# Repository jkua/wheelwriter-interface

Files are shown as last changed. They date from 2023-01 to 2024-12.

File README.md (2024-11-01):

# Low-level IBM Wheelwriter interface
This project is to build a low-level interface for an IBM Wheelwriter 
typewriter. This builds on work by 
[tofergregg](https://github.com/tofergregg/IBM-Wheelwriter-Hack), 
[RussellSenior](https://github.com/tofergregg/IBM-Wheelwriter-Hack/pull/11), 
and [jim11662418](https://github.com/jim11662418/wheelwriter-teletype) 
who figured out the internal serial communication bus and the protocol it uses.

This project was built and tested on an IBM Wheelwriter 3. Likely this will 
work on at least Series I Wheelwriters (3/5/6), and possibly later models as 
well.

## Architecture
This project consists of:

1. [Hardware interface module](pcb/) - this attaches to the back of the Wheelwriter as
the OEM printer option did, and connect to the 10-pin option connector located 
behind the 70 mm-wide hinged panel on the top rear of the typewriter. The core 
electronics are an [Arduino Nano RP2040 Connect](https://docs.arduino.cc/hardware/nano-rp2040-connect)
mounted on a custom PCB to interface with the Wheelwriter's option connector. 

3. [Arduino Wheelwriter driver](src/arduino/wheelwriter_interface) - this 
communicates with the Wheelwriter over the serial bus and provide low-level 
control of the typewriter, including platen and carriage positioning and 
typehead imprinting.

4. [REST API](docs/wwib_rest_api.md) service - the built-in WiFi connectivity 
on the Nano supports a web server which allows a modern computer, smartphone, 
or tablet to control the typewriter via the interface module.

5. [Python serial client](src/client) - PC client to talk to the Arduino and
allow it to send text to print as well as relay raw Wheelwriter commands. 

6. REST Client software - this software will demonstrate the use of the REST API

## Related work
[IBM-Wheelwriter-Hack](https://github.com/tofergregg/IBM-Wheelwriter-Hack) by 
Chris Gregg/[tofergregg](https://github.com/tofergregg) is what initially 
inspired me to look into Wheelwriters. His [videos](https://www.youtube.com/watch?v=Awxbu8y5cv8) 
[on](https://www.youtube.com/watch?v=0vrvDQmZcPI) 
[YouTube](https://www.youtube.com/watch?v=5FTS4fj5Im4) showed his work on 
reverse engineering the Wheelwriter's bus with a logic analyzer in about 2017.
His implementation bit-bangs a TX line to drive a N-channel MOSFET.

Be sure to check out his 
[Smith Corona typewriter to printer conversion](https://www.youtube.com/watch?v=le4C2HeNrdQ)!

Ryan Jarvis/[Cabalist](https://github.com/Cabalist) provided a 
[complete printwheel mapping](https://github.com/tofergregg/IBM-Wheelwriter-Hack/issues/5) 
for US language printwheels.

[Russell Senior](https://github.com/RussellSenior) made the connection that 
this is an Intel 8051 9-bit serial bus in mode 2 and provided a 
[great wiki page](https://github.com/RussellSenior/IBM-Wheelwriter-Hack/wiki/Bus-Protocol) 
describing a great deal of the command set.

[jim11662418](https://github.com/jim11662418) created implementations for 
the 8051 compatible [Dallas Semi DS89C440](https://github.com/jim11662418/wheelwriter-printer)
and [STC Micro STC15W4K32S4](https://github.com/jim11662418/wheelwriter-teletype)
that are very nice.

[MicroCoreLabs](https://github.com/MicroCoreLabs) created an 
[Lattice FPGA implementation](https://github.com/MicroCoreLabs/Projects/tree/master/Wheelwriter) 
and an [Arduino Leonardo implementation](https://github.com/MicroCoreLabs/Projects/tree/master/Wheelwriter2). 
Both implement a serial port that translates an ASCII character stream to motor 
controller commands. The Arduino implementation directly uses the ATmega32u4's 
UART an interestingly toggles the transmitter off when not sending. 
[Here's a YouTube video](https://www.youtube.com/watch?v=q8gCYw75E1A) of the 
FPGA version running.

[CadetWriter](https://github.com/IBM-1620/Cadetwriter) is an effort by Dave 
Babcock and Stephen Casner to interface to a Wheelwriter 1000 by instead 
sitting between the keyboard and the logic controller. This work was developed 
to build a general-purpose ASCII terminal.

[Generative Daily Planner](https://www.thingswemake.com/generative-daily-planner)
([Github](https://github.com/joshsucher/wheelwriter-gpt-agenda)) by Josh 
Sucher, is a "GPT-4-powered bot that ingests email, calendar and contacts from 
a range of sources (mainly Gmail, Gcal and iCloud) and outputs a daily agenda" 
and utilizes code from this repo.

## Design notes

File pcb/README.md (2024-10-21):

# Wheelwriter Interface Board

There are two versions of the Wheelwriter Interface Board. 

## v1 - Prototype breadboard
v1 ([schematic](wwib-v1/wwib-v1_schematic.pdf)) is the original prototype and 
was wired up on a solderless breadboard. This is what the code base was 
developed on as of 2024-09-21. This design is based on 
[tofergregg's](https://github.com/tofergregg/IBM-Wheelwriter-Hack) work.

## v2 - Expansion housing PCB
v2 ([schematic](wwib-v2/WheelwriterInterfaceBoard_schematic.pdf)) was designed 
to be a fabricated PCB and be the same size as the original Wheelwriter 
expansion boards, fit in the original expansion housing, and connect to the 
Wheelwriter expansion interface connector via a cable. This design has and 
isolated power supply and bus interface and is powered by the typewriter 
instead of the Arduino's USB port. 

*While I have not tested this design, [BlipRanger](https://github.com/BlipRanger)
has [reported success](https://github.com/jkua/wheelwriter-interface/issues/2#issuecomment-2415313493)!*

### Expansion cable
The expansion port on the Wheelwriter is a Molex SL series 10-pin shrouded 
header. A short cable needs to be built to connect the Wheelwriter expansion 
port to this interface board. A mating connector is Molex 50-57-9210 
(70066-0079). Contacts for 22-24 AWG wire are Molex 16-02-0102 (70058-0222). 

This design only uses +5V (pins 1, 2), GND (pins 3, 4), and BUS (pin 5). The 
rest are only for testing.

### v2 mounted in expansion housing
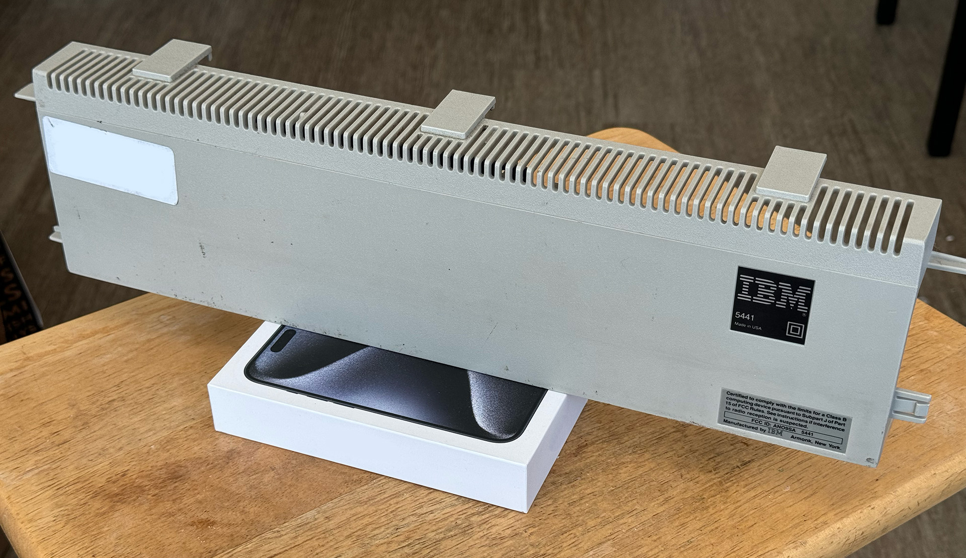
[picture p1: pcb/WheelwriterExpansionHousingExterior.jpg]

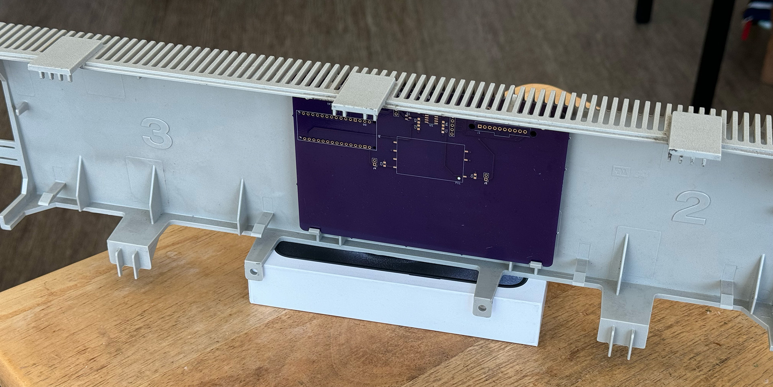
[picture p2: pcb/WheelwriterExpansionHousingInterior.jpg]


## Reference
### Original Wheelwriter expansion board
Image of the back of the board
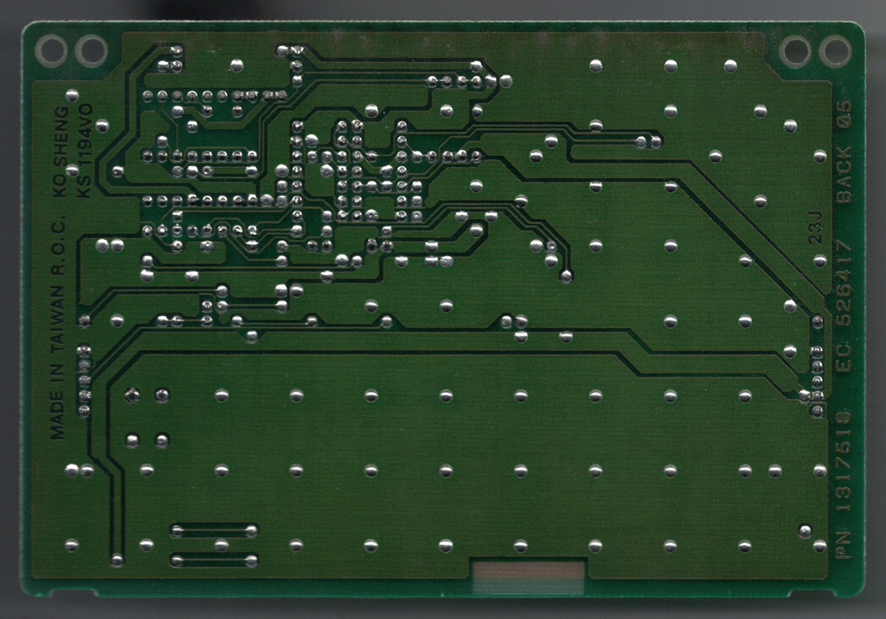
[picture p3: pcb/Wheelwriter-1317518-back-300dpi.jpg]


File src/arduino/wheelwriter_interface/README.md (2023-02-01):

# Arduino Nano RP2040 Connect Wheelwriter Interface
This programs an Arduino Nano RP2040 to communicate with an IBM Wheelwriter 3/5/6.

## Serial UART
The IBM Wheelwriter serial bus is the Intel 8051 serial port in mode 2. This 
operates at 187500 baud (12 MHz / 64), 9 data bits, no parity, 1 stop bit. 
The 9th bit is used to indicate that this is an address (1) or data (0).

While the RP2040 built-in UART and the underlying mbed OS supports Mark/Space 
(Forced0/Forced1) parity, the Arduino SDK does not seem to support it. 
Modifying the board package Serial.cpp to set the Forced0/Forced1 parity mode 
causes the board to stop functioning.

To get around this, a PIO-based 9-bit UART was implemented, based on the 
Raspberry Pi Pico PIO UART example.

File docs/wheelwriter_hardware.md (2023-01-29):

# Wheelwriter 3 Hardware

                           ┌─────────────────┐         ┌────────────┐   ┌──────────────┐
                           │                 │         │            │   │              │
                           │                 │         │  Platen    │   │              │
                           │    Typehead     │         │  Position  │   │    Power     │
                           │    Carrier      │◄────┐   │  Stepper   │   │    Supply    │
                           │                 │     │   │  Motor     │   │    Board     │
                           │                 │     │   │            │   │              │
                           │                 │     │   └─────────▲──┘   │              │
                           └─────────────────┘     │             │      └──────┬───────┘
                                                   │             │             │
                                                   │             │             │
                                                   │             │             │
                           ┌──────────────────┐    │       ┌─────┴─────────────▼───────┐         ┌───────────────┐
    ┌──────────────┐       │                  │    │       │    J3P           J6P      │         │               │
    │              │       │                  │    └───────┤J4P                        │         │               │
    │              ├──────►│J1F               │            │         Motor             │         │               │
    │   Keyboard   │       │      Logic       │            │         Control           │         │   Option      │
    │              │       │      Board    J8F├───────────►│J5P      Board          J1P│◄────────┤   Connector   │
    │              ├──────►│J2F               │            │                           │         │               │
    └──────────────┘       │                  │            │                           │         │               │
                           │   J5F            │            │          J2P              │         │               │
                           └────┬─────────────┘            └───────────┬───────────────┘         └───────────────┘
    ┌──────────────┐            │                                      │
    │              │            │                                      │
    │ Panel Lights │◄───────────┘                                ┌─────▼──────┐
    │              │                                             │            │
    └──────────────┘                                             │  Carrier   │
                                                                 │  Position  │
                                                                 │  Stepper   │
                                                                 │  Motor     │
                                                                 │            │
                                                                 └────────────┘

## Logic board (1356782-05)
This is powered by an Intel P8051AH operating at 11.9 MHz. This interfaces with 
the keyboard via a pair of flex cables, the panel lights, and the motor control 
board. This is where the central processing occurs, accepting input from the 
keyboard and outputting commands to the motor control board via serial bus.

Logic board to Motor control board (J8F, 7-pin AMP cable, black)
1. VRM - Voltage regulator module? 5.1VDC
2. PDI - ?
3. BRQ - Bus request?
4. BUS - Serial communication bus (187500 bps, 9-N-1, 5V, idle high)
5. GND - Ground
6. POR - Power on reset?
7. +5  - 5VDC

Logic board to Panel lights (J5F, 10-pin AMP cable, black)
1. +5
2. LTB
3. LTC
4. LTD
5. LTE
6. LTF
7. LTG
8. LTH
9. LTI
10. LTJ

Keyboard to Logic board (J1F, 13 pin flex)
Keyboard to Logic board (J2F, 15 pin flex, 9 pins not connected)

## Motor control board (FRONT BRD - 1356776-09, attached )
This is powered by an Intel P8051AH operating at 12 MHz. This receives commands 
from the logic and option boards to drive the typehead carrier, the carrier 
position stepper motor, and the platen position stepper motor. It also 
distributes power from the power supply board.

Motor control board to Option (J1P, 10-pin)
1. +5  - +5VDC
2. +5  - +5VDC
3. GND - Ground
4. GND - Ground
5. BUS - Serial communication bus (187500 bps, 9-N-1, 5V, idle high)
6. *NC* - Not connected 
7. BRQ - Bus request?
8. POR - Power on reset?
9. VRM - Voltage regulator module? 
10. PDI - ?

Motor control board to Carrier position stepper motor (J2P, 6-pin AMP, black)
1. EA+
2. EC
3. EB+
4. EA
5. EC+
6. EB

Motor control board to Platen position stepper motor (J3P, 6-pin AMP, multicolor)
1. ID
2. IB
3. IC
4. IA
5. IBD
6. IAC

Motor control board to Typehead carrier (J4P, 22-pin (11x2))
1. HMR
2. HMR
3. SA+
4. SC
5. SB+
6. SA
7. SC+
8. SB
9. LEDG
10. LEDA
11. GND
12. LA
13. LC
14. LB
15. LD
16. FA
17. FC
18. FB
19. FD
20. SENG
21. SENS
22. SE+5

Motor control board to Logic board (J5P, 9-pin, AMP)
1. +34
2. GND
3. VRM
4. PDI
5. BRQ
6. BUS
7. GND
8. FPOR
9. +5

Motor control board to Power supply (J6P, 8-pin)
1. VRM
2. GND
3. -5
4. GND
5. +5
6. +15
7. GND
8. +34

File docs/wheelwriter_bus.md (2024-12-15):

# Wheelwriter bus
The Wheelwriter bus is a shared +5V serial line operating at 187,500 bps 
(12 MHz/64), with 9 data bits and 1 stop bit. This is likely the Intel 8051
serial port operating in mode 2. See the description on page 3-14 of the 
[Intel 8051 datasheet](http://datasheets.chipdb.org/Intel/MCS51/MANUALS/27238302.PDF). 
The 9th bit is used as to indicate the transmitted byte is an address if the 
bit if 1 and data if the bit is 0.

## Implementation
Many embedded devices don't actually implement a 9-bit serial port, but instead 
use the parity bit to implement this. Many have "sticky" or "stick" parity 
modes which override a transmitted parity bit. Sometimes this is referred to as 
"mark" parity to send/expect a 1 or "space" parity to send/expect a 0. Embedded 
devices often will interrupt when the parity bit indicates when an address byte 
is sent.

However, while the RP2040 built-in UART supports this mode, the Arduino SDK 
does not appear to support it. Using these modes causes the board to stop 
functioning. Instead, a 9-bit PIO-based UART was implemented. See 
[src/arduino/wheelwriter_interface/README.md](src/arduino/wheelwriter_interface/README.md)
for more information.

## Protocol
[Bus protocol](https://github.com/RussellSenior/IBM-Wheelwriter-Hack/wiki/Bus-Protocol) 
as reverse engineered by [RussellSenior](https://github.com/RussellSenior).

The motor controller appears to be address `0x21`.

The basic protocol for communicating with the motor controller is to send 

`<address> <command> <optional data 1> <optional data 2>`

where each element is one byte. Each byte is acknowledged by the motor 
controller, such that this looks like (`<client> (controller)`):

`<address> (ACK) <command> (ACK/response) <optional data 1> (ACK) <optional data 2> (ACK)`

where `ACK` is simply `0x00`. For query commands, the controller will send a 
`response` byte rather than an `ACK`. 

As this is a half-duplex bus, the client must allow for the `ACK`s by either 
monitoring the bus for these responses or inserting a long delay (~450 ms to be 
safe). Failure to do so will result in garbled communication as the controller 
responses will step on the client transmissions. Some implementations simply 
wait for the bus to go low and then high again to detect the ACKs. Coupled with 
an additional delay in case the response is non-zero, this should be a reliable 
method.

However, this interface reads the motor controller replies in order to properly 
understand the query responses. Looking at the logic board output, it prepends 
any type or movement command with a status query. Likely this is to ensure that 
the carriage and platen have stopped moving before issuing the next type or 
movement command.

### Commands
| Command | Data 1 | Data 2 | Response | Description |
|---|---|---|---|---|
| `0x00`  | - | - | `0x06`: Wheelwriter 3 | Query model, returns model byte |
| | | | `0x25`: Wheelwriter 5 | |
| | | | `0x26`: Wheelwriter 6 | |
| `0x01`  | - | - | Wheel pitch (see command `0x08`) | Power-on reset, moves to left stop, returns wheel pitch |
| `0x02`  | `wheel_position` | `IGNORED` | `0x00` | Type character without advancing |
| `0x03`  | `wheel_position` | `uspaces` | `0x00` | Type character and advance carriage to the right |
| `0x04`  | `wheel_position` | `uspaces` | `0x00` | Type on erase ribbon and advance carriage to the right |
| `0x05`  | bit 7: `dir` (0: paper down, 1 up) | - | `0x00` | Rotate platen |
| | bits 0-6: `usteps` | - | | |
| `0x06`  | bit 7: `dir` (0: left, 1 right) | `usteps_low`  | `0x00` | Move carriage |
| | bits 0-6: `usteps_high` | | | |
| `0x07`  | - | - | `0x00` | Spin wheel |
| `0x08`  | - | - | `0x08`: Proportional  | Query printwheel pitch |
| | | | `0x10`: 15 cpi | |
| | | | `0x20`: 12 cpi | |
| | | | `0x21`: No wheel | |
| | | | `0x40`: 10 cpi | |
| `0x09`  | `impression_ctrl`| - | `0x00` | Sets the hammer strike power. On a Wheelwriter 3 this is `0x00` or `0x01`. Later models (WW10) appear to have three levels. Also set with Code+Q |
| `0x0a`  | `0x00` | - | `0x00` | Unknown - emitted during power up after power-on reset command |
| `0x0b`  | - 	 | - | `0x00`: Ready | Query status - sent prior to all typing and motion commands |
| | | | `0x04`: Carriage moving? | |
| | | | `0x07`: Carriage move complete? | |
| | | | `0x10`: Platen moving?| |
| | | | `0x14`:	 | |
| | | | `0x40`: Printwheel changed or left limit switch pressed | |
| `0x0c`  | `keypressed` | `0x46`: Start keypress event  | `0x04`, `0x10` | Sent prior to typing/motion commands |
| | | `0x08`: Backspace and some space events | `0x010`, `0xf0` at left margin | Sent after typing/motion command and before `0x44` |
| | | `0x44`: Wait for motion? | `0x40`, `0x80` | Sent after typing/motion command - can take a long time to get response |
| | | `0x06`: End keypress event | `0x04`, `0x10`, `0x39` | Last query of typing/motion command set - fast response |
| | | `0x01`: Wait for platen/carriage move | UNKNOWN | Sent after platen/tab commands |
| `0x0d`  | 

### Typing command sequence
 1. Query status - `0x0b` / `0x00`
 2. Query - `0x0c` `keypressed` `0x46` / variable
 3. Type and advance - `0x03` `wheel_position` `uspaces` / `0x00`
 4. (rare) Query - `0x0c` `keypressed` `0x08` / variable
 5. Query - `0x0c` `keypressed` `0x44` / variable
 6. Query - `0x0c` `keypressed` `0x06` / variable
 ### Return command sequence
 1. Query status - `0x0b` / `0x00`
 2. Move platen - `0x05`
 3. Move carriage - `0x06`
 4. Query - `0x0c` `0x56` (return key) `0x01` / `0x20`
 ### Tab command sequence
 Note that pressing the space bar uses the typing command sequence above
 1. Query status - `0x0b` / `0x00`
 2. Move carriage - `0x06`
 3. Query - `0x0c` `0x4a` (tab) `0x01` / `0x20`
 ### Platen command sequence (paper up/down)
 1. Query status - `0x0b` / `0x00`
 2. Move platen - `0x05`
 3. Query - `0x0c` `keypressed` (return key) `0x01` / `0x20`
 ### Power on sequence
 1. Power-on reset - `0x01` / `0x20`
 2. Unknown - `0x0a` `0x00` / `0x00`
 3. Query - `0x0c` `0x00` `0x01` / `0x20`
 4. Move carriage right 120 uspaces (1") - `0x06` `0x80` `0x78` / `0x00`

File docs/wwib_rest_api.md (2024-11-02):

# Wheelwriter Interface Board REST API

This describes the REST API that allows access to Wheelwriter functions.

## Endpoints:
Note that parameters are sent as a comma-separated list.
* `/` (**GET**) - returns a simple web page
* `/type` (**POST**) - send an ASCII file to this endpoint and the typewriter will 
type it. Supports the same ANSI/CSI-style escape codes that the [serial console](wwib_serial_protocol.md) 
does.
* `/query` (**POST**) - responds with a JSON listing the Wheelwriter model, 
printwheel pitch, and status
* `/characterTest` (**POST**) - types all the characters on the printwheel
* `/circleTest` (**POST**) - types `Lorem ipsum` in a circle
* `/printwheelSample` (**POST**) - types a formatted printwheel sample
* `/readLine` (**POST**) - reads a line of text from the typewriter. This will 
wait for a carriage return. There is a configurable timeout in milliseconds 
from the last typed character. The terminating newline is included. By default, 
backspace characters are not included and the corrected line is returned.
	* timeout (int) - the number of milliseconds after the last character 
	entered to wait for return to be pressed. 0 (default) waits indefinitely
	* corrected (bool) - return the corrected line. Default is 1. If 0, the 
	uncorrected line in returned, including backspace characters.

## Setup
Use the serial console to setup the WiFi with the `wifi` command. The IP address 
will be listed and you should get a simple web page if you access that in a 
browser. Currently only DHCP is supported for IP address configuration.

## Examples
* `curl -X POST http://<ip_address>/type -d "test1234"` causes your Wheelwriter to type `test1234`
* `curl -X POST http://<ip_address>/type -d "test^[[1m1234"` will output the same, but `1234` will be bold
* `curl -X POST http://<ip_address>/type --data-binary "@<filename>"` to send a text file
* `curl -X POST http://<ip_address>/query` returns something like `{"model":6,"wheel":32,"status":0}`

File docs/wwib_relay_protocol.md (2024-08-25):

# Wheelwriter Interface Board Command Relay Protocol
This binary protocol is used to have the interface board relay raw commands to 
the typewriter and the responses back. This mode also supports sending batches 
of commands.

## Commands (client to interface board)
All commands, except for NOOP (0x0a) and end relay mode (0x04) will return a response.

### Special commands (0x0N)

#### NOOP (0x0a, 1 byte)
* Format: `\n`

Nothing happens. Typically, this is a command terminator, but if no command has 
been started, the interface board will ignore additional/duplicate values.

#### End relay mode (0x04, 1 byte)
* Format: `\d`

Ends relay mode and returns.

### Relay command (0x1N)
Used to relay commands to the typewriter.

The structure of a relay command is the following sequence of bytes:
* `<relay_flags> <ww_dest_addr> <ww_command> <ww_data_1> <ww_data_2>\n`
	* `<relay_flags>` identifies that this is a relay command and sets certain 
		operating modes. See below for more information.
	* `<ww_dest_addr`> is the Wheelwriter address to relay the command to. 
		Typically this is 0x21.
	* `<ww_command>` is the Wheelwriter command
	* `<ww_data_1>` is the first data byte for the Wheelwriter command. If the 
		command does not accept an argument, this is ignored.
	* `<ww_data_2>` is the second data byte for the Wheelwriter command. If the 
		command does not accept an argument, this is ignored.

Structure of the `relay_flags` byte (8 bits): 
* `<relay_command (0 0 0 1) | <reserved (0)> <ignore_errors_flag> <batch_flag> <abbreviated_command_flag>`
	* `abbreviated_command_flag`, when set, indicates that destination address 
	    should be the configured destination. See the **set destination address** 
	    configuration command for more information.
	* `batch_flag`, when set, indicates that a batch of commands will be sent in 
		a single transaction.
		* The batch format is: `<command_byte> <# commands (1 byte)> <command_0> <command_1> ... <command_2>\n`
		* If `abbreviated_command_flag` is set, the commands will not include the destination address.
	* `ignore_errors_flag`, when set, tells the interface board to ignore any errors and send blindly.
	* `reserved` must be 0

The following are usage examples:

#### Single command - full, halt on error (0x10, 6 bytes)
* Format: `0x10 <address (1 byte)> <command (1 byte)> <data1 (1 byte)> <data2 (1 byte)> \n`
* Example: `0x10 0x21 0x03 0x01 0x0a 0x0a`

This sends the command (0x03) to type a character (0x01, first position on the 
typewheel), and then advance the carriage (0x0a) spaces.

If any byte of the command is not acknowledged by the typewriter before the 
timeout, the error code will be set in the response.

#### Batched commands - full, halt on error (0x12, 4n+4 bytes)
* Format: `0x12 <# commands (2 bytes)> <full command 1 (4 bytes)> <full command 2 (4 bytes)> ... <full command n (4 bytes)>\n`

If any byte of any command is not acknowleged by the typewriter before the 
timeout, the interface board will stop sending commands and return 
`batch_failed` with the index of the failed command.

#### Single command - full, ignore errors (0x14, 6 bytes)
* Format: `0x14 <address (1 byte)> <command (1 byte)> <data1 (1 byte)> <data2 (1 byte)> \n`
* Example: `0x14 0x21 0x03 0x01 0x0a 0x0a`

With the `ignore_errors_flag` set, the interface board will continue sending 
command bytes, even if not acknowledged. Configure the timeout value to control 
how long the interface board should wait for a response before continuing.

#### Batched commands - full, ignore errors (0x16, 4n+4 bytes)
* Format: `0x16 <# commands (2 bytes)> <full command 1 (4 bytes)> <full command 2 (4 bytes)> ... <full command n (4 bytes)>\n`

With the `ignore_errors_flag` set, the interface board will continue sending 
command bytes, even if not acknowledged. Configure the timeout value to control 
how long the interface board should wait for a response before continuing.

#### Single command - abbreviated, halt on error (0x11, 5 bytes)
* Format: `0x11 <command (1 byte)> <data1 (1 byte)> <data2 (1 byte)> \n`
* Example: `0x01 0x03 0x01 0x0a 0x0a`

In this mode, the Wheelwriter destination address is not sent and the default 
value (motor control board, 0x21) is used. This can be changed at runtime with 
the **set destination address** configuration command. 

#### Batched commands - abbreviated, halt on error (0x13, 3n+4 bytes)
* Format: `0x13 <# commands (2 bytes)> <abbreviated command 1 (3 bytes)> <abbreviated command 2 (3 bytes)> ... <abbreviated command n (3 bytes)>\n`

In this mode, the Wheelwriter destination address is not sent and the default 
value (motor control board, 0x21) is used. This can be changed at runtime with 
the **set destination address** configuration command. 

### Configuration commands (0xcN, 0xdN)
Used to configure relay parameters.

The structure of a query/configuration command is the following sequence of bytes:
* Parameter query (2 bytes): `<query_command (0xdN)> \n`
* Parameter config (3 bytes): `<config_command (0xeN)> <value> \n`

Structure of the `query_command` / `config_command` byte (8 bits): 
* `<config_command_flag (1)> <reserved (1)> <reserved (1)> <get/set> | <parameter (4 bits)>`
	* `<parameter>` specifies the parameter to be configured or queried
		* 0x00: Wheelwriter destination address (default: 0x21)
		* 0x01: Command timeout in milliseconds (default: 100 (0x64))

#### Get destination address (0xd0, 2 bytes)
* Format: `0xd0 \n`

This returns the current address. The `response_status` will be **parameter 
query success** (0xd0) and `parameter_value` will be the address.

#### Set destination address (0xe0, 3 bytes)
* Format: `0xe0 <address (1 byte)> \n`
* Example (set address to `0xab`): `0xe0 0xab 0x0a`

This changes the destination address until the interface board is power-cycled, 
at which time it returns to the default. The `response_status` will be 
**parameter config success** (0xe0) and `parameter_value` will be the new 
address.

#### Get command timeout (0xd1, 2 bytes)
* Format: `0xd1 \n`

This returns the current timeout in milliseconds. The `response_status` will 
be **parameter query success** (0xd0) and `parameter_value` will be the 
timeout value.

#### Set command timeout (0xe1, 3 bytes)
* Format: `0xe1 <address (1 byte)> \n`
* Example (set timeout to 200 ms): `0xe1 0xc8 0x0a`

This changes the destination address until the interface board is power-cycled, 
at which time it returns to the default. The `response_status` will be 
**parameter config success** (0xe0) and `parameter_value` will be the new 
timeout.

## Response (interface board to client) (4 bytes)
* Format: `<command_responding_to> <response_status> <typewriter_reply/error_data/parameter_value> \n`
	* `<command_responding_to>` indicates the command that the interface board is replying to

### Response statuses
* Reserved: 0x0N
* Relay reponses:
	* 0x10 - Success
		* `typewriter_reply` contains the typewriter's response
	* 0x11 - NACK/timeout - typewriter command was not acknowleged before timeout 
		* `error_data` is the index of the command byte which was not acknowledged (zero-indexed)
	* 0x12 - Batch failed
		* `error_data` is the index of the command which failed (zero-indexed)
	* 0x13 - Invalid typewriter command - the command to be relayed is invalid
		* `error_data` is the index of the command which failed (zero-indexed)
* Parameter query responses: 0xdN
	* 0xd0 - Parameter query success
	* 0xd1 - Parameter query failed
	* 0xd3 - Invalid parameter
		* `error_data` contains the command byte
* Parameter config responses: 0xeN
	* 0xe0 - Parameter config success
	* 0xe1 - Parameter config failed
	* 0xe3 - Invalid parameter
		* `error_data` contains the command byte
* General error responses: 0xfN
	* 0xf0 - Invalid command
		* `error_data` contains the command byte
	* 0xf1 - Invalid command length
		* `error_data` contains the expected length
	* 0xf2 - Command receive timeout - the full command including the 
		terminating `\n`, was not received before the timeout.
		* `error_data` contains the command byte
	* 0xff - Panic - things have gone off the rails

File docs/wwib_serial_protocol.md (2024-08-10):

# Wheelwriter Interface Board Serial Communication Protocol

This describes the serial communication protocol between a client and the 
Wheelwriter Interface Board (WWIB).

This is implemented in [src/arduino/wheelwriter_interface/wheelwriter_interface.ino](../src/arduino/wheelwriter_interface/wheelwriter_interface.ino).

## Serial port parameters
The WWIB communicates using serial over USB at a baud rate of 115200 with 
software flow control (XON/XOFF).

## Character encoding and line endings
This protocol uses ASCII with line feeds (`\n`) to end lines.

## Main loop
On power up, the WWIB starts the main loop and outputs:

```
### Wheelwriter Interface ###
[READY]
```

The `[READY]` prompt indicates that the WWIB is ready to accept one of the 
following primary commands:

1. `help` - print the help text, listings these commands
2. `buffer` - execute the buffer test
3. `char` - execute the character test
4. `circle` - execute the circle test
5. `keyboard` - read input from the keyboard
6. `loopback` - execute the loopback test
7. `query` - query typewriter for information
8. `raw` - raw command mode
9. `read` - read bus commands
10. `sample` - print a type sample
11. `type` - type characters on the typewriter

Some commands accept parameters - these are separated by spaces. The full 
command string, including parameters, are sent terminated with a line feed (`\n`).

e.g. `buffer 10 80\n`

### Buffer test
* *Command:* `buffer <numChars> <charsPerLine>`
* *Arguments:* 
    1. `numChars` - number of characters to send (default 10)
    2. `charsPerLine` - number of characters per line (default 80)

This tests the interface boards ability to send character to the Wheelwriter. It 
repeatedly sends the sequence `123456789.` until it reaches the specified number 
of characters to send (`numChars`). `charsPerLine` specifies the number of 
characters per line.

This returns to the main loop after completion.

### Character test
* *Command:* `char <typestyle>`
* *Arguments:* 
    1. `typestyle` - typestyle to use [`bold`, `underline`]. (default `normal`)

This exercises all the characters on the typewheel in US keyboard order. The 
typestyle may be specified to test the bold and underline modes.

This returns to the main loop after completion.

### Circle test
* *Command:* `circle`
* *Arguments:* None

This tests the ability of the WWIB to use discrete carriage and platen movement 
commands to type the string `Hello, world! Lorem ipsum dolor sit amet.` in a 
circle.

This returns to the main loop after completion.

### Keyboard mode
* *Command:* `keyboard`
* *Arguments:*
    1. `verbose` - supports two levels of verbosity (`v`, `vv`) beyond the default

In this mode, the Wheelwriter keyboard is read and the keypresses are output. 
This mode assumes that the Wheelwriter is using a US keyboard layout.

This mode does not suppress the actual typing that the Wheelwriter does.

The WWIB starts by sending `[BEGIN]` and then listening for keyboard input. 
When a keypress is detected, the ASCII value is output. 

In `v` verbosity mode, each keypress is sent as a hexadecimal value on a 
separate line. e.g. `Keypress: 0x61`

In `vv` verbosity mode, in addition to the above, the line `NO_KEYPRESS` is 
output if no keypress is detected.

Sending `q` or EOT/`^D`/`0x24` will end the capture and return to the main 
loop.

### Loopback test
* *Command:* `loopback`
* *Arguments:* None

This performs a simple low level test of Wheelwriter bus communication by 
continuously sending a query command one byte at a time and listening for 
ACKs/responses after each byte.

Sending `q` or EOT/`^D`/`0x24` will end the test and return to the main 
loop.

### Query test
* *Command:* `query`
* *Arguments:* None

This uses the high level API to query the model, printwheel pitch, and status of 
the Wheelwriter.

This returns to the main loop after completion.

### Raw mode
* *Command:* `raw`
* *Arguments:* None

In this mode, raw commands may be relayed to the Wheelwriter. 

The WWIB starts by outputting `[BEGIN]`.

Each command is accepted as 1-3 bytes, represented as space separated numeric 
strings, terminated with a line feed (`\n`). The prefix `0x` may be used to 
specify hexadecimal values, otherwise they are assumed to be decimal values.

e.g. `0x121 0x00\n` sends the query command (`0x00`) to address (`0x121`)

Sending `q` or EOT/`^D`/`0x24` will end this mode and return to the main 
loop.

### Read mode (bus sniffer)
* *Command:* `read`
* *Arguments:* None

In this mode, the WWIB listens for communications on the Wheelwriter bus.

The WWIB starts by outputting `[BEGIN]`. Then it outputs each command sequence 
that it hears on the bus.

Sending `q` or EOT/`^D`/`0x24` will end this mode and return to the main 
loop.

### Sample mode
* *Command:* `sample <plusPosition> <underscorePosition>`
* *Arguments:*
    1. `plusPosition` - the position of the `+` character on the printwheel
    2. `underscorePosition` - the position of the `_` character on the printwheel

This types a sample of text which exercises all 96 characters of the printwheel, 
in a regular pattern (16 x 6) along with alignment marks intended for scanning 
and automatic image processing. 

This returns to the main loop after completion.

### Type mode
* *Command:* `type <keyboard> <useCaratAsControl>`
* *Arguments:*
    1. `keyboard` - set the keyboard (default `1` for US)
    2. `useCaratAsControl` - uses the `^` symbol as a control character for
        escaping commands.

In this mode, ASCII strings sent to the WWIB are typed on the Wheelwriter. 
[ANSI escape](https://en.wikipedia.org/wiki/ANSI_escape_code) style codes are 
supported to set various typing modes. The escape character is sent as `0x1b` or 
with the `^[` if `useCaratAsControl` is set. The latter is useful when 
composing documents in a text editor.

The escape codes follow the CSI (Control Sequence Introducer) `[` with the 
[SGR (Select Graphic Rendition) parameter](https://en.wikipedia.org/wiki/ANSI_escape_code#SGR_(Select_Graphic_Rendition)_parameters) format:

`<ESC><CSI><n>m`

*Supported escape codes*
* Normal: `^[[0m`
* Bold: `^[[1m`
* Underline: `^[[4m`
* Single space: `^[[10m`
* 1.5 space: `^[[11m`
* Double space: `^[[12m`
* Triple space: `^[[13m`
* Not bold: `^[[22m`
* Not underline: `^[[24m`

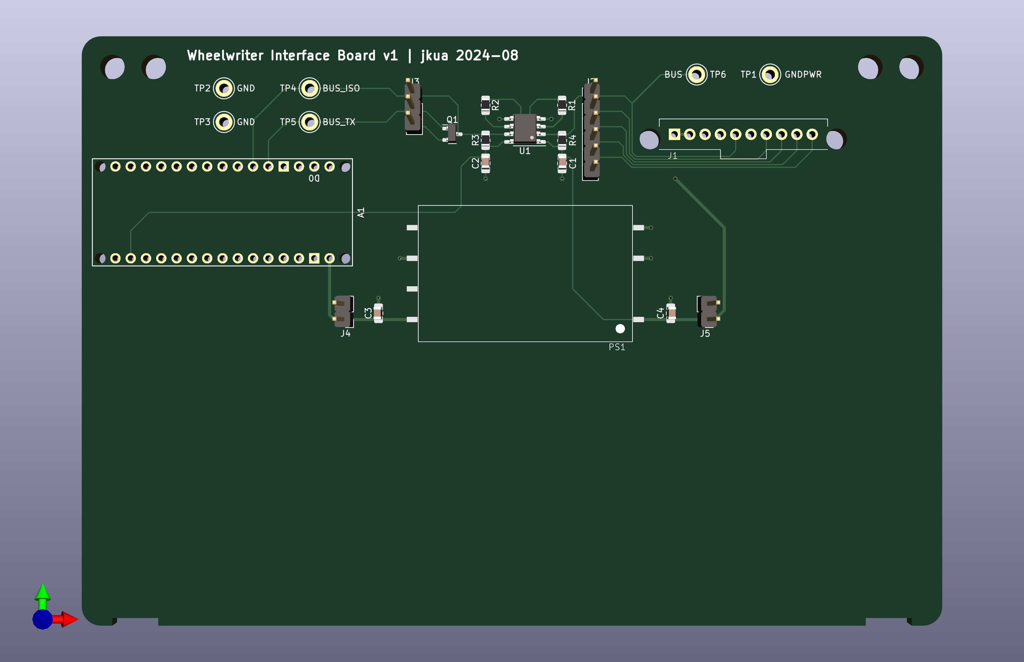
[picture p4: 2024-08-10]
pcb/wwib-v2/WheelwriterInterfaceBoard_pcb.png

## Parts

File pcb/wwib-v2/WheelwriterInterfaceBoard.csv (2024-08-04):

Source: | /Users/jkua/Dropbox/Projects/wheelwriter-interface/pcb/WheelwriterInterfaceBoard.kicad_sch
Date: | Sunday, August 04, 2024 at 02:24:00 PM
Tool: | Eeschema 7.0.9
Generator: | /Applications/KiCad/KiCad.app/Contents/SharedSupport/plugins/bom_csv_grouped_by_value.py
Component Count: | 27
Collated Components:
Item | Qty | Reference(s) | Value | LibPart | Footprint | Datasheet | DNP
1 | 1 | A1 | Arduino_Nano_RP2040_Connect_Socket | PCM_arduino-library:Arduino_Nano_RP2040_Connect_Socket | PCM_arduino-library:Arduino_Nano_Every_Socket | https://docs.arduino.cc/hardware/nano-rp2040-connect
2 | 2 | C1, C2 | 0.1uF, 16V | Device:C | Capacitor_SMD:C_0805_2012Metric_Pad1.18x1.45mm_HandSolder | ~
3 | 2 | C3, C4 | 10uF, 16V | Device:C | Capacitor_SMD:C_0805_2012Metric_Pad1.18x1.45mm_HandSolder | ~
4 | 4 | H1, H2, H3, H4 | MountingHole | Mechanical:MountingHole | MountingHole:MountingHole_160mil | ~
5 | 1 | J1 | Conn_01x10 | Connector_Generic:Conn_01x10 | Connector_Molex_JK:Molex SL 70541-0009 | ~
6 | 1 | J2 | Conn_01x06 | Connector_Generic:Conn_01x06 | Connector_PinHeader_2.54mm:PinHeader_1x06_P2.54mm_Vertical | ~
7 | 1 | J3 | Conn_01x03 | Connector_Generic:Conn_01x03 | Connector_PinHeader_2.54mm:PinHeader_1x03_P2.54mm_Vertical | ~
8 | 2 | J4, J5 | Conn_01x02 | Connector_Generic:Conn_01x02 | Connector_PinHeader_2.54mm:PinHeader_1x02_P2.54mm_Vertical | ~
9 | 1 | PS1 | ~ | Regulator_Switching:CC10-0505Sx-E | Converter_DCDC:Converter_DCDC_TDK-Lambda_CC10(R)
10 | 1 | Q1 | 2N7002 | Transistor_FET:2N7002 | Package_TO_SOT_SMD:SOT-23 | https://www.onsemi.com/pub/Collateral/NDS7002A-D.PDF
11 | 4 | R1, R2, R3, R4 | 4.7K | Device:R_US | Resistor_SMD:R_0805_2012Metric_Pad1.20x1.40mm_HandSolder | ~
12 | 6 | TP1, TP2, TP3, TP4, TP5, TP6 | TestPoint | Connector:TestPoint | TestPoint:TestPoint_Keystone_5005-5009_Compact | ~
13 | 1 | U1 | ISO1540 | Isolator:ISO1540 | Package_SO:SOIC-8_3.9x4.9mm_P1.27mm | http://www.ti.com/lit/ds/symlink/iso1541.pdf

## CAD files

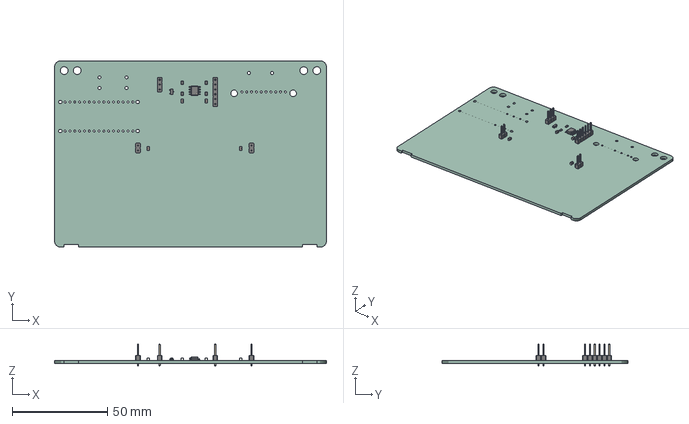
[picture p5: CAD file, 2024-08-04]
pcb/wwib-v2/WheelwriterInterfaceBoard.step
142.9 x 97.8 x 11.5 mm
WheelwriterInterfaceBoard PCB

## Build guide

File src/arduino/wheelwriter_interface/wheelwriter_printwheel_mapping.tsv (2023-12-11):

Wheel Address | 001 (US) |  | 026,029 (Germany) |  | 067,253 (UK?) |  | 070 (Spain) |  | 103 (ASCII) |  | 200,201 (Symbol 1) |  | 202 (Symbol 2) |  | 203 (Symbol 3) |  | 231 (USSR)
 | Character | ASCII | Character | ASCII | Character | ASCII | Character | ASCII | Character | ASCII | Character | ASCII | Character | ASCII | Character | ASCII | Character | ASCII
00 | <space> | 20 | <space> | 20 | <space> | 20 | <space> | 20 | <space> | 20 | <space> | 20 | <space> | 20 | <space> | 20 | <space> | 20
01 | a | 61 | a | 61 | a | 61 | a | 61 | a | 61 |  |  |  |  |  |  | а | 0430
02 | n | 6E | n | 6E | n | 6E | n | 6E | n | 6E |  |  |  |  |  |  | н | 043D
03 | r | 72 | r | 72 | r | 72 | r | 72 | r | 72 |  |  |  |  |  |  | р | 0440
04 | m | 6D | m | 6D | m | 6D | m | 6D | m | 6D |  |  |  |  |  |  | м | 043C
05 | c | 63 | c | 63 | c | 63 | c | 63 | c | 63 |  |  |  |  |  |  | ц | 0446
06 | s | 73 | s | 73 | s | 73 | s | 73 | s | 73 |  |  |  |  |  |  | с | 0441
07 | d | 64 | d | 64 | d | 64 | d | 64 | d | 64 |  |  |  |  |  |  | д | 0434
08 | h | 68 | h | 68 | h | 68 | h | 68 | h | 68 |  |  |  |  |  |  | х | 0445
09 | l | 6C | l | 6C | l | 6C | l | 6C | l | 6C |  |  |  |  |  |  | л | 043B
0A | f | 66 | f | 66 | f | 66 | f | 66 | f | 66 |  |  |  |  |  |  | ф | 0444
0B | k | 6B | k | 6B | k | 6B | k | 6B | k | 6B |  |  |  |  |  |  | к | 043A
0C | , | 2C | , | 2C | , | 2C | , | 2C | , | 2C |  |  |  |  |  |  | , | 2C
0D | V | 56 | V | 56 | V | 56 | V | 56 | V | 56 |  |  |  |  |  |  | В | 0412
0E | - | 2D | - | 2D | - | 2D | - | 2D | - | 2D |  |  |  |  |  |  | - | 2D
0F | G | 47 | G | 47 | G | 47 | G | 47 | G | 47 |  |  |  |  |  |  | Г | 0413
10 | U | 55 | U | 55 | U | 55 | U | 55 | U | 55 |  |  |  |  |  |  | У | 0423
11 | F | 46 | F | 46 | F | 46 | F | 46 | F | 46 |  |  |  |  |  |  | Ф | 0424
12 | B | 42 | B | 42 | B | 42 | B | 42 | B | 42 |  |  |  |  |  |  | Б | 0411
13 | Z | 5A | Z | 5A | Z | 5A | Z | 5A | Z | 5A |  |  |  |  |  |  | З | 0417
14 | H | 48 | H | 48 | H | 48 | H | 48 | H | 48 |  |  |  |  |  |  | Х | 0425
15 | P | 50 | P | 50 | P | 50 | P | 50 | P | 50 |  |  |  |  |  |  | П | 041F
16 | ) | 29 | ) | 29 | ) | 29 | ) | 29 | ) | 29 |  |  |  |  |  |  | ) | 29
17 | R | 52 | R | 52 | R | 52 | R | 52 | R | 52 |  |  |  |  |  |  | Р | 0420
18 | L | 4C | L | 4C | L | 4C | L | 4C | L | 4C |  |  |  |  |  |  | Л | 041B
19 | S | 53 | S | 53 | S | 53 | S | 53 | S | 53 |  |  |  |  |  |  | С | 0421
1A | N | 4E | N | 4E | N | 4E | N | 4E | N | 4E |  |  |  |  |  |  | Н | 041D
1B | C | 43 | C | 43 | C | 43 | C | 43 | C | 43 |  |  |  |  |  |  | Ц | 0426
1C | T | 54 | T | 54 | T | 54 | T | 54 | T | 54 |  |  |  |  |  |  | Т | 0422
1D | D | 44 | D | 44 | D | 44 | D | 44 | D | 44 |  |  |  |  |  |  | Д | 0414
1E | E | 45 | E | 45 | E | 45 | E | 45 | E | 45 |  |  |  |  |  |  | Е | 0415
1F | I | 49 | I | 49 | I | 49 | I | 49 | I | 49 |  |  |  |  |  |  | И | 0418
20 | A | 41 | A | 41 | A | 41 | A | 41 | A | 41 |  |  |  |  |  |  | А | 0410
21 | J | 4A | J | 4A | J | 4A | J | 4A | J | 4A |  |  |  |  |  |  | Й | 0419
22 | O | 4F | O | 4F | O | 4F | O | 4F | O | 4F |  |  |  |  |  |  | О | 041E
23 | ( | 28 | ( | 28 | ( | 28 | ( | 28 | ( | 28 |  |  |  |  |  |  | ( | 28
24 | M | 4D | M | 4D | M | 4D | M | 4D | M | 4D |  |  |  |  |  |  | М | 041C
25 | . | 2E | ` | 60 | . | 2E | ` | 60 | . | 2E |  |  |  |  |  |  | Ч | 0427
26 | Y | 59 | Y | 59 | Y | 59 | Y | 59 | Y | 59 |  |  |  |  |  |  | Ы | 042B
27 | , | 2C | ´ | B4 | , | 2C | ´ | B4 | , | 2C |  |  |  |  |  |  | Э | 042D
28 | / | 2F | / | 2F | / | 2F | / | 2F | / | 2F |  |  |  |  |  |  | / | 2F
29 | W | 57 | W | 57 | W | 57 | W | 57 | W | 57 |  |  |  |  |  |  | Ж | 0416
2A | 9 | 39 | 9 | 39 | 9 | 39 | 9 | 39 | 9 | 39 |  |  |  |  |  |  | 9 | 39
2B | K | 4B | K | 4B | K | 4B | K | 4B | K | 4B |  |  |  |  |  |  | К | 041A
2C | 3 | 33 | 3 | 33 | 3 | 33 | 3 | 33 | 3 | 33 |  |  |  |  |  |  | 3 | 33
2D | X | 58 | X | 58 | X | 58 | X | 58 | X | 58 |  |  |  |  |  |  | Ь | 042C
2E | 1 | 31 | 1 | 31 | 1 | 31 | 1 | 31 | 1 | 31 |  |  |  |  |  |  | 1 | 31
2F | 2 | 32 | 2 | 32 | 2 | 32 | 2 | 32 | 2 | 32 |  |  |  |  |  |  | 2 | 32
30 | 0 | 30 | 0 | 30 | 0 | 30 | 0 | 30 | 0 | 30 |  |  |  |  |  |  | 0 | 30
31 | 5 | 35 | 5 | 35 | 5 | 35 | 5 | 35 | 5 | 35 |  |  |  |  |  |  | 5 | 35
32 | 4 | 34 | 4 | 34 | 4 | 34 | 4 | 34 | 4 | 34 |  |  |  |  |  |  | 4 | 34
33 | 6 | 36 | 6 | 36 | 6 | 36 | 6 | 36 | 6 | 36 |  |  |  |  |  |  | 6 | 36
34 | 8 | 38 | 8 | 38 | 8 | 38 | 8 | 38 | 8 | 38 |  |  |  |  |  |  | 8 | 38
35 | 7 | 37 | 7 | 37 | 7 | 37 | 7 | 37 | 7 | 37 |  |  |  |  |  |  | 7 | 37
36 | * | 2A | * | 2A | * | 2A | * | 2A | * | 2A |  |  |  |  |  |  | Ю | 042E
37 | $ | 24 | $ | 24 | $ | 24 | $ | 24 | $ | 24 |  |  |  |  |  |  | ¤ | A4
38 | # | 23 | # | 23 | # | 23 | Ñ | D1 | # | 23 |  |  |  |  |  |  | э | 044D
39 | % | 25 | % | 25 | % | 25 | % | 25 | % | 25 |  |  |  |  |  |  | % | 0025
3A | ¢ | A2 | ü | FC | µ | B5 | ¿ | BF | ^ | 5E |  |  |  |  |  |  | ю | 044E
3B | + | 2B | + | 2B | + | 2B | + | 2B | + | 2B |  |  |  |  |  |  | + | 2B
3C | ± | B1 | Ü | DC | ± | B1 | ¨ | A8 | ` | 60 |  |  |  |  |  |  | щ | 0449
3D | @ | 40 | Ä | C4 | @ | 40 | · | B7 | @ | 40 |  |  |  |  |  |  | Ё | 0401
3E | Q | 51 | Q | 51 | Q | 51 | Q | 51 | Q | 51 |  |  |  |  |  |  | Я | 042F
3F | & | 26 | & | 26 | & | 26 | & | 26 | & | 26 |  |  |  |  |  |  | & | 0026
40 | ] | 5D | ß | DF | ] | 5D | ¡ | A1 | ] | 5D |  |  |  |  |  |  | ъ | 044A
41 | [ | 5B | µ | B5 | [ | 5B | º | BA | [ | 5B |  |  |  |  |  |  | Ъ | 042A
42 | ³ | B3 | ³ | B3 | ³ | B3 | Ç | C7 | \ | 5C |  |  |  |  |  |  | ³ | 00B3
43 | ² | B2 | ² | B2 | ² | B2 | ç | E7 | | | 7C |  |  |  |  |  |  | ² | 00B2
44 | ° | B0 | ° | B0 | ° | B0 | ª | AA | ~ | 7E |  |  |  |  |  |  | Щ | 0429
45 | § | A7 | § | A7 | < | 3C | < | 3C | < | 3C |  |  |  |  |  |  | § | A7
46 | ¶ | B6 | Ö | D6 | £ | A3 | > | 3E | > | 3E |  |  |  |  |  |  | ч | 0447
47 | ½ | BD | ö | F6 | ½ | BD | ñ | F1 | } | 7D |  |  |  |  |  |  | ш | 0448
48 | ¼ | BC | ä | E4 | > | 3E | ̂ | 0302 | { | 7B |  |  |  |  |  |  | Ш | 0428
49 | ! | 21 | ! | 21 | ! | 21 | ! | 21 | ! | 21 |  |  |  |  |  |  | ! | 21
4A | ? | 3F | ? | 3F | ? | 3F | ? | 3F | ? | 3F |  |  |  |  |  |  | ? | 3F
4B | " | 22 | " | 22 | " | 22 | " | 22 | " | 22 |  |  |  |  |  |  | " | 22
4C | ' | 27 | ' | 27 | ' | 27 | ' | 27 | ' | 27 |  |  |  |  |  |  | № | 2116
4D | = | 3D | = | 3D | = | 3D | = | 3D | = | 3D |  |  |  |  |  |  | = | 003D
4E | : | 3A | : | 3A | : | 3A | : | 3A | : | 3A |  |  |  |  |  |  | : | 003A
4F | _ | 5F | _ | 5F | _ | 5F | _ | 5F | _ | 5F |  |  |  |  |  |  | _ | 005F
50 | ; | 3B | ; | 3B | ; | 3B | ; | 3B | ; | 3B |  |  |  |  |  |  | ё | 0451
51 | x | 78 | x | 78 | x | 78 | x | 78 | x | 78 |  |  |  |  |  |  | ь | 044C
52 | q | 71 | q | 71 | q | 71 | q | 71 | q | 71 |  |  |  |  |  |  | я | 044F
53 | v | 76 | v | 76 | v | 76 | v | 76 | v | 76 |  |  |  |  |  |  | в | 0432
54 | z | 7A | z | 7A | z | 7A | z | 7A | z | 7A |  |  |  |  |  |  | з | 0437
55 | w | 77 | w | 77 | w | 77 | w | 77 | w | 77 |  |  |  |  |  |  | ж | 0436
56 | j | 6A | j | 6A | j | 6A | j | 6A | j | 6A |  |  |  |  |  |  | й | 0439
57 | . | 2E | . | 2E | . | 2E | . | 2E | . | 2E |  |  |  |  |  |  | . | 002E
58 | y | 79 | y | 79 | y | 79 | y | 79 | y | 79 |  |  |  |  |  |  | ы | 044B
59 | b | 62 | b | 62 | b | 62 | b | 62 | b | 62 |  |  |  |  |  |  | б | 0431
5A | g | 67 | g | 67 | g | 67 | g | 67 | g | 67 |  |  |  |  |  |  | г | 0433
5B | u | 75 | u | 75 | u | 75 | u | 75 | u | 75 |  |  |  |  |  |  | у | 0443
5C | p | 70 | p | 70 | p | 70 | p | 70 | p | 70 |  |  |  |  |  |  | п | 043F
5D | i | 69 | i | 69 | i | 69 | i | 69 | i | 69 |  |  |  |  |  |  | и | 0438
5E | t | 74 | t | 74 | t | 74 | t | 74 | t | 74 |  |  |  |  |  |  | т | 0442
5F | o | 6F | o | 6F | o | 6F | o | 6F | o | 6F |  |  |  |  |  |  | о | 043E
60 | e | 65 | e | 65 | e | 65 | e | 65 | e | 65 |  |  |  |  |  |  | е | 0435

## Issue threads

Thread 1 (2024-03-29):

How to build the Hardware interface module?

treefrog911, 2024-03-29:
Would love to try this project on my Wheelwriter but I can't find any info at all on the actual hardware required to interface the Pi to the Wheelwriter (the "Hardware interface module"). Can you help?

jkua, 2024-08-20:
Hi! Sorry, my work on this is quite intermittent. If you're still interested, I added schematics for the [hardware interface module here](https://github.com/jkua/wheelwriter-interface/tree/main/pcb). v1 is what I've been using.

Closed 2024-08-20.

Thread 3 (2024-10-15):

REST/Serial over wifi

BlipRanger, 2024-10-15:
This issue is just to check in on the current state of / discuss the REST api implementation. Is the plan to essentially run a REST server which can call the same commands exposed via serial?

jkua, 2024-10-17:
Unfortunately REST support currently doesn't exist; it is merely a figment of my imagination. That said, it sounds like a good weekend project, so I might take a look this weekend.

I'd be interested to hear what you're looking for in such an interface. My thinking was that this would a convenient way for smartphones, tablets, and other devices on the network to talk to the typewriter.

My initial thought for implementation was to provide REST calls for the some of the various functions currently implemented:

1. `type` would be a good first candidate as you can just send it ASCII + escape sequences and it will print it
2. `relay` would certainly be powerful, but developers would need to port some/all of Wheelwriter.h in order to use it.
3. `read` and `keyboard` seems messy for REST. You'd have to poll to get data
4. `query`, `sample`, and the tests `buffer`, `char`, `circle` would be fine. The tests probably have limited utility

A lock would need to be implemented so that commands from multiple users, whether serial or REST, won't step on each other

jkua, 2024-11-01:
I've implemented initial REST support! This supports the following POST endpoints:

1. `/type` - send an ASCII file to this endpoint and the typewriter will type it. Supports the same [ANSI/CSI-style escape codes](https://github.com/jkua/wheelwriter-interface/blob/rest-v1/src/arduino/wheelwriter_interface/Wheelwriter.cpp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) that the serial console does.
2. `/query` - responds with a JSON listing the Wheelwriter model, printwheel pitch, and status
3. `/characterTest`, `/circleTest`,  and `/printwheelSample`

If you install [rest-v1](https://github.com/jkua/wheelwriter-interface/tree/rest-v1), you can use the serial console to setup the WiFi with the `wifi` command. The IP address will be listed and you should get a simple web page if you access that in a browser.

* `curl -X POST http://<ip_address>/type -d "test1234"` should cause your Wheelwriter to type `test1234`
* `curl -X POST http://192.168.2.87/type -d "test^[[1m1234"` will output the same, but `1234` will be bold
* `curl -X POST http://<ip_address>/type --data-binary "@<filename>"` to send a text file
* `curl -X POST http://<ip_address>/query` should return something like `{"model":6,"wheel":32,"status":0}`

jkua, 2024-11-02:
Hmm, I could implement a read function that waits for a carriage return. I can see the utility in that.

It would be blocking, just as all the other functions are, but I'll add a timeout parameter. It would only listen for keyboard entry during the read command, sorta half-duplex. Full duplex communication would probably require a man-in-the-middle setup and a running input buffer.

I'll see if I can implement that this morning!

jkua, 2024-11-02:
OK, I added `/readLine` in [rest-v1.2](https://github.com/jkua/wheelwriter-interface/tree/rest-v1.2) - this reads a line until return is pressed.

There is a configurable `timeout` (sent in the [POST request to the endpoint](https://github.com/jkua/wheelwriter-interface/blob/rest-v1.2/docs/wwib_rest_api.md)) that sets a timeout in integer milliseconds from the last key pressed, so that if someone partially enters a line and never hits return, you'll get it.

By default, you'll get the corrected line if the user backspaces. You can set the `corrected` parameter to `0` to get the uncorrected line with backspace characters included if you want to see what the user edited.

Let me know what you think!

jkua, 2024-11-17:
Yeah, I've got a good idea why that's happening. I suspect it has to do with how I interpret reverse carriage movement commands as backspace and platen movement as line feed. I'm actually working on a direct way to get the key pressed, rather than this indirect way of looking at movement commands, but that's a larger change.

I can probably write a patch, but before I do, what version of the code are you using?

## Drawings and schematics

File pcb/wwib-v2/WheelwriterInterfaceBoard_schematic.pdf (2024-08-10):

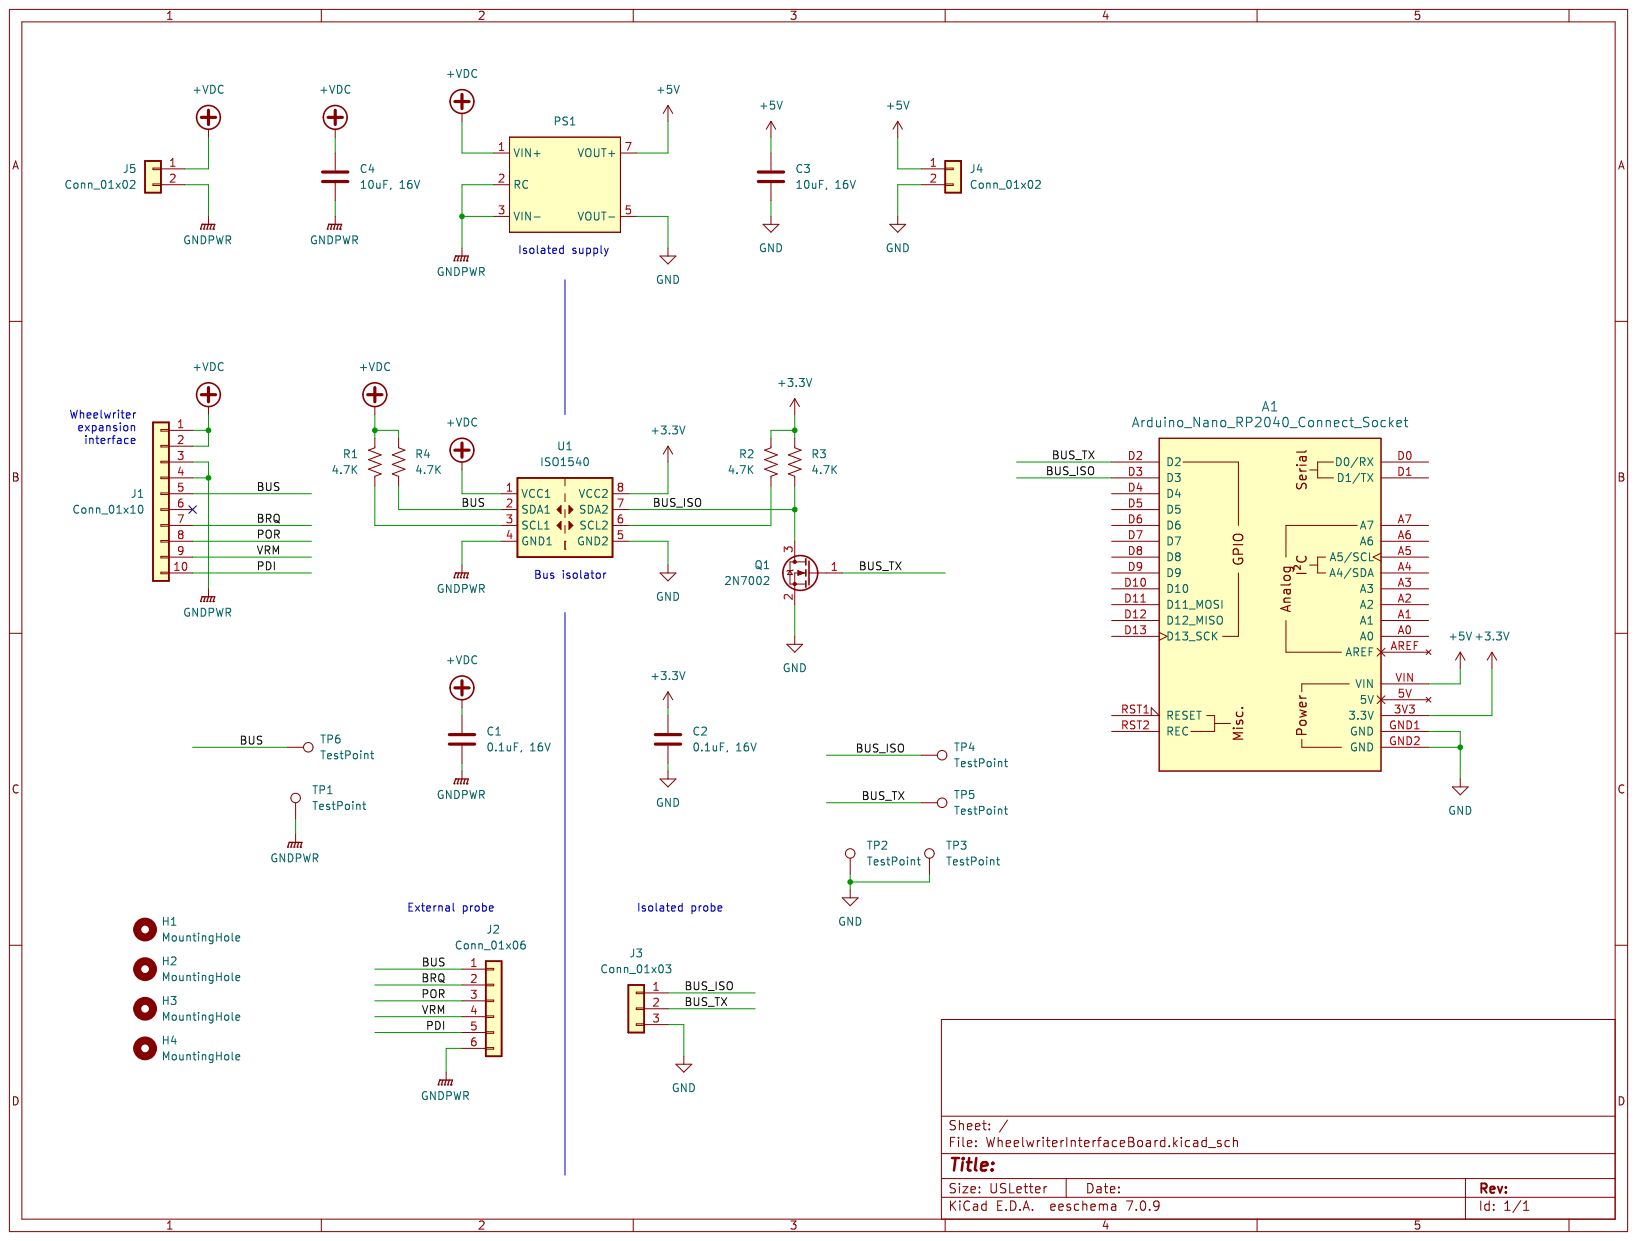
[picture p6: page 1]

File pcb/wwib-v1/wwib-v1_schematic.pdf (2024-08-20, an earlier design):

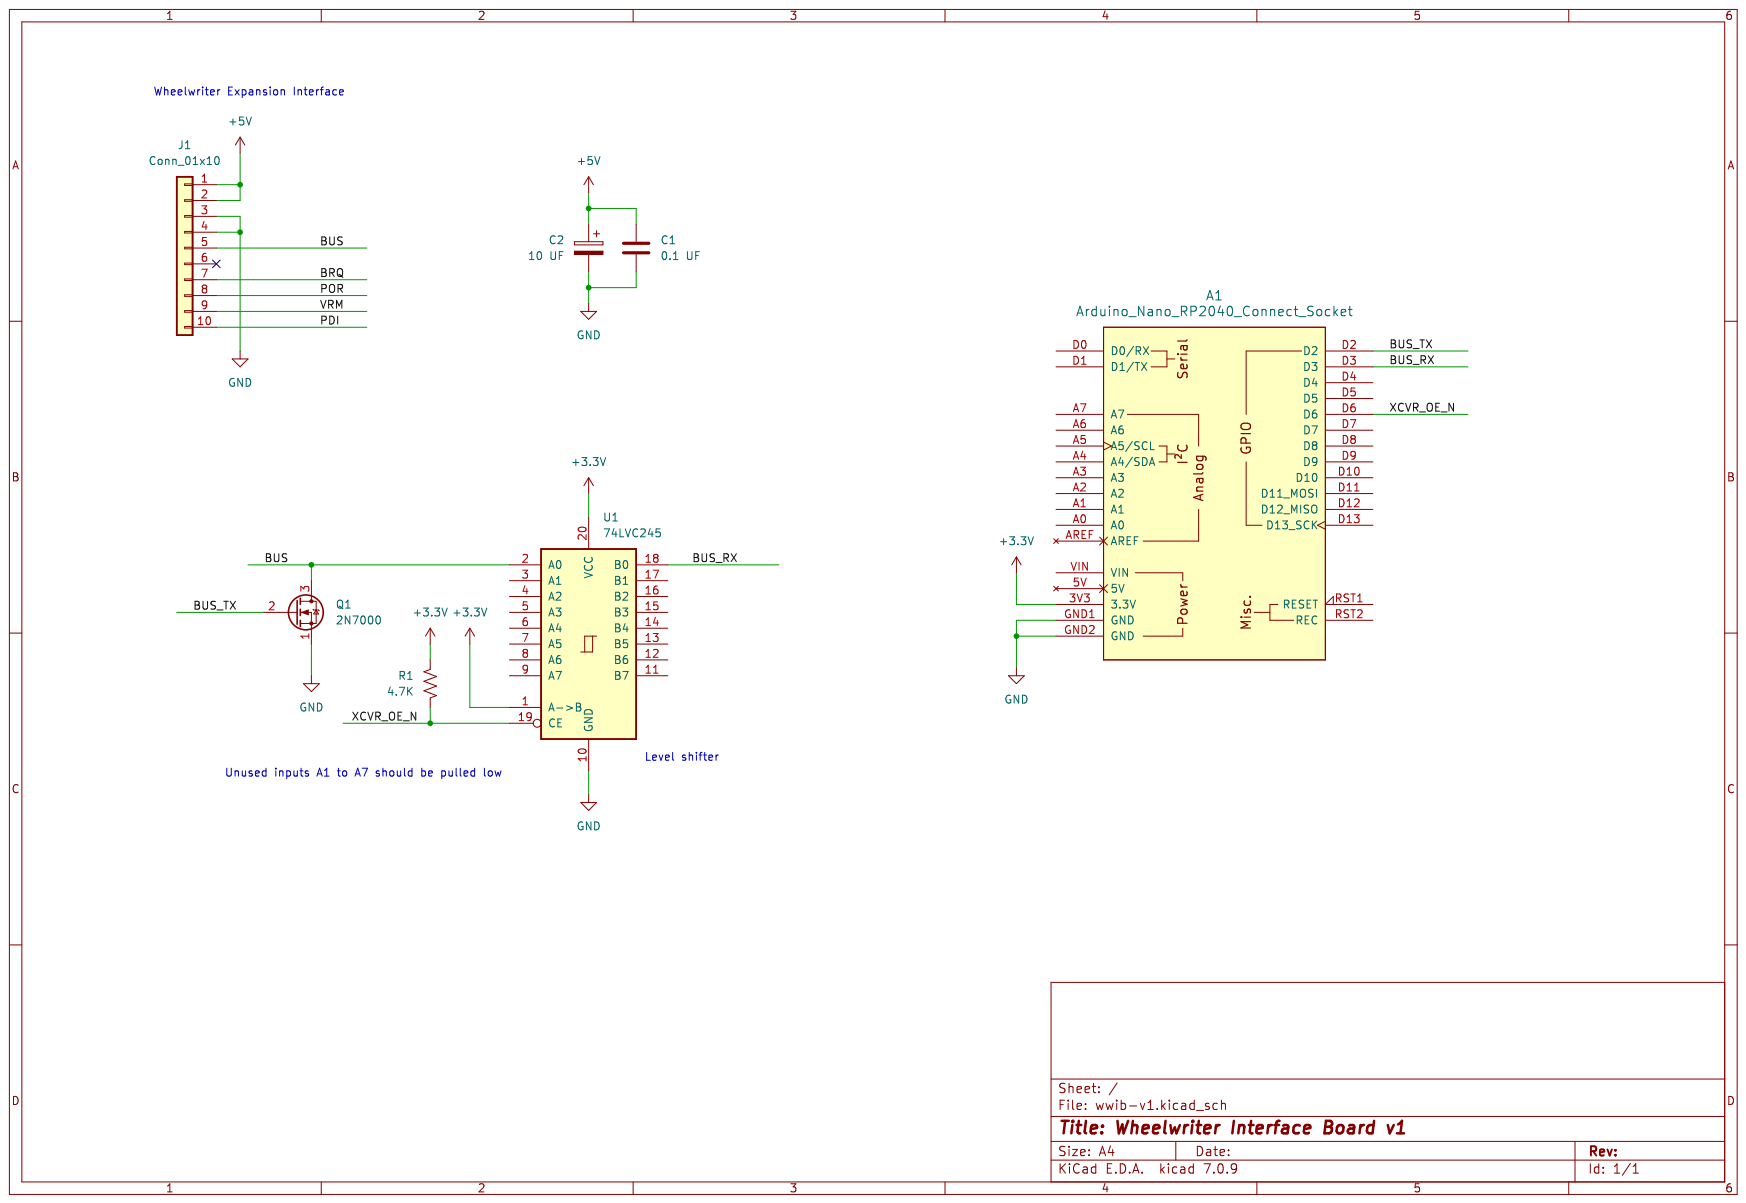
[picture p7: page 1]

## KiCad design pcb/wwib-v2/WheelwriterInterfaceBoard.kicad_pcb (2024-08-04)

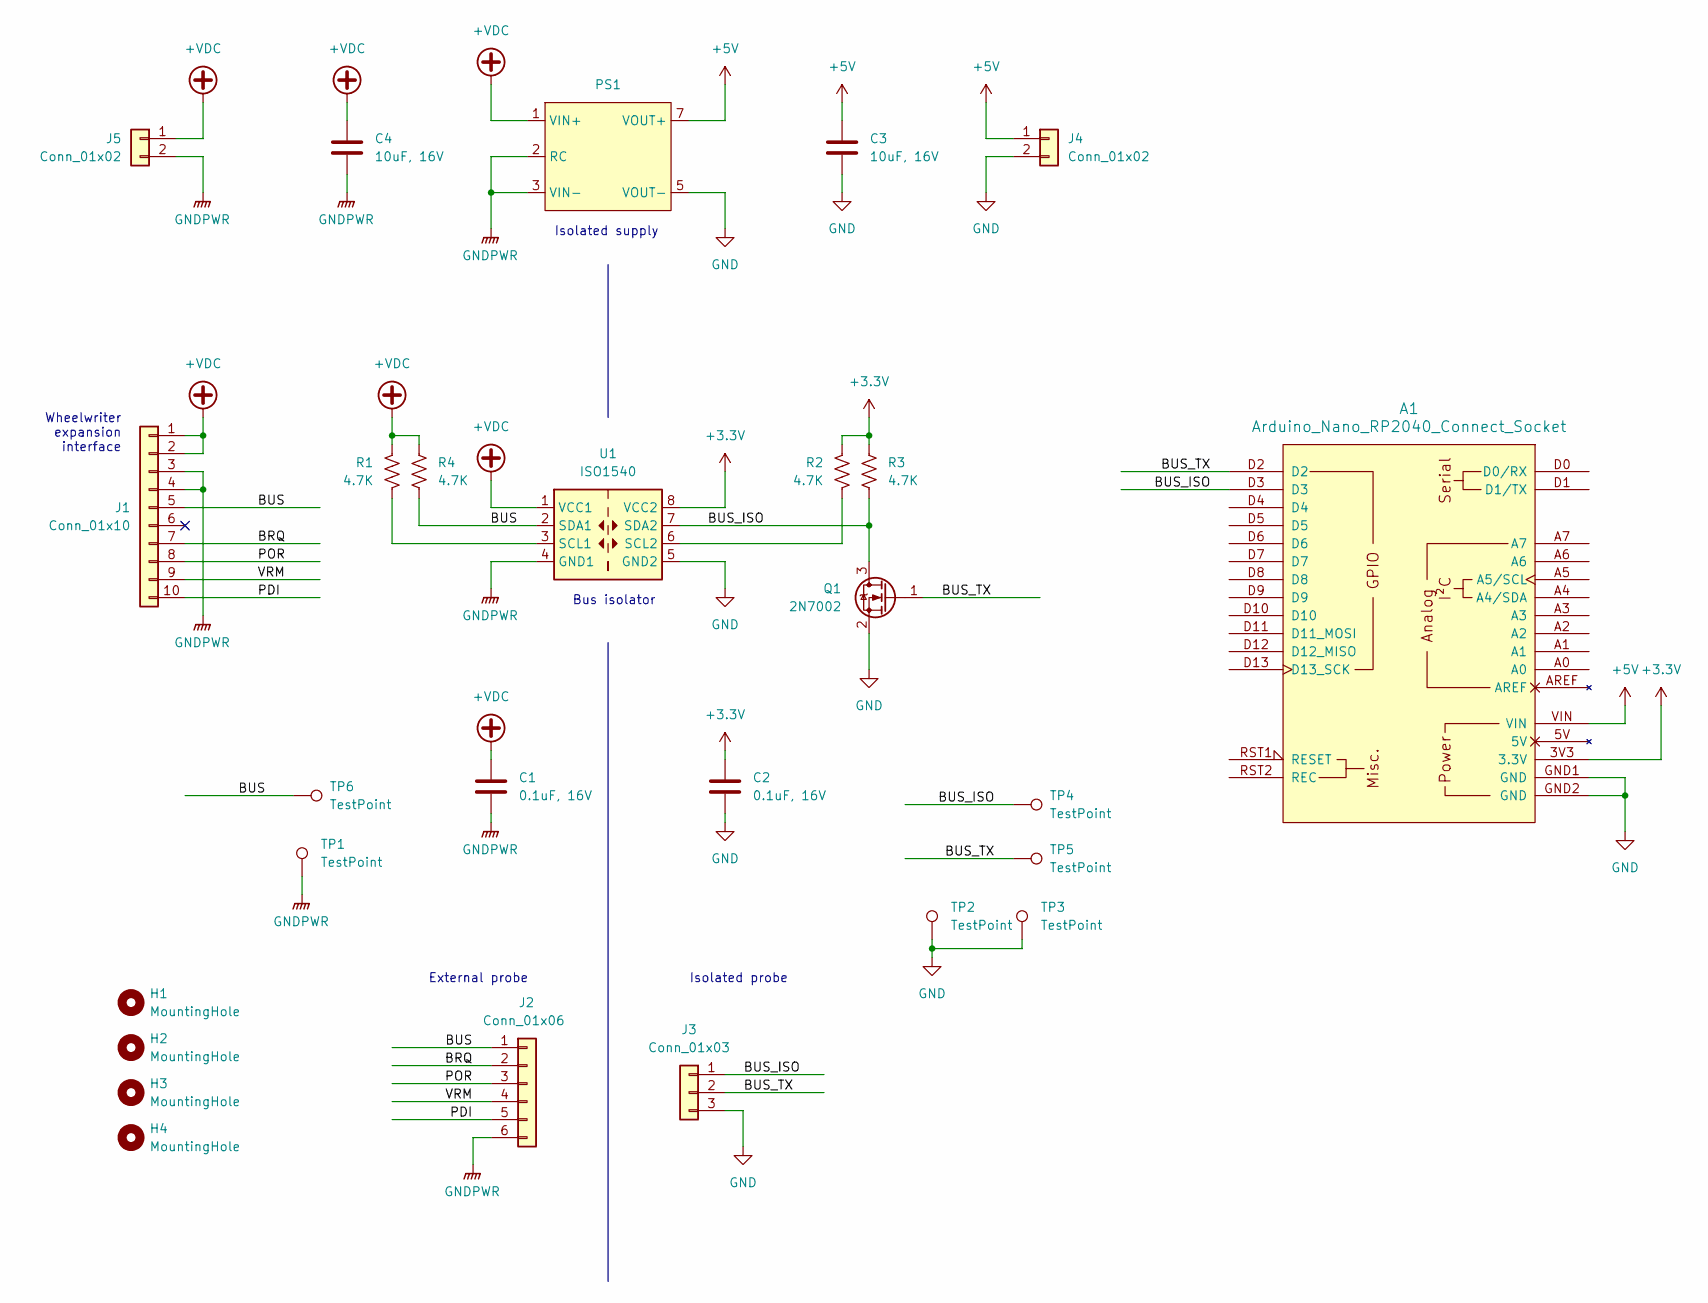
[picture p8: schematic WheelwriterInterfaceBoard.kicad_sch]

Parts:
A1: Arduino_Nano_RP2040_Connect_Socket; Arduino_Nano_Every_Socket
C1, C2: 0.1uF, 16V; C_0805_2012Metric_Pad1.18x1.45mm_HandSolder
C3, C4: 10uF, 16V; C_0805_2012Metric_Pad1.18x1.45mm_HandSolder
H1, H2, H3, H4: MountingHole; MountingHole_160mil
J1: Conn_01x10; Molex SL 70541-0009
J2: Conn_01x06; PinHeader_1x06_P2.54mm_Vertical
J3: Conn_01x03; PinHeader_1x03_P2.54mm_Vertical
J4, J5: Conn_01x02; PinHeader_1x02_P2.54mm_Vertical
PS1: Converter_DCDC_TDK-Lambda_CC10(R)
Q1: 2N7002; SOT-23
R1, R2, R3, R4: 4.7K; R_0805_2012Metric_Pad1.20x1.40mm_HandSolder
TP1, TP2, TP3, TP4, TP5, TP6: TestPoint; TestPoint_Keystone_5005-5009_Compact
U1: ISO1540; SOIC-8_3.9x4.9mm_P1.27mm

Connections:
+3.3V: A1.3V3 (3.3V), C2.1, R2.1, R3.1, U1.8 (VCC2)
+5V: A1.VIN, C3.1, J4.1, PS1.7 (VOUT+)
+VDC: C1.1, C4.1, J1.1, J1.2, J5.1, PS1.1 (VIN+), R1.1, R4.1, U1.1 (VCC1)
/BRQ: J1.7, J2.2
/BUS: J1.5, J2.1, R4.2, TP6.1, U1.2 (SDA1)
/BUS_ISO: A1.D3, J3.1, Q1.3 (D), R3.2, TP4.1, U1.7 (SDA2)
/BUS_TX: A1.D2, J3.2, Q1.1 (G), TP5.1
/PDI: J1.10, J2.5
/POR: J1.8, J2.3
/VRM: J1.9, J2.4
GND: A1.GND1 (GND), A1.GND2 (GND), C2.2, C3.2, J3.3, J4.2, PS1.5 (VOUT-), Q1.2 (S), TP2.1, TP3.1, U1.5 (GND2)
GNDPWR: C1.2, C4.2, J1.3, J1.4, J2.6, J5.2, PS1.2 (RC), PS1.3 (VIN-), TP1.1, U1.4 (GND1)
unnamed: R1.2, U1.3 (SCL1)
unnamed: R2.2, U1.6 (SCL2)

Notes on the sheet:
External probe
Bus isolator
Isolated supply
Wheelwriter expansion interface
Isolated probe

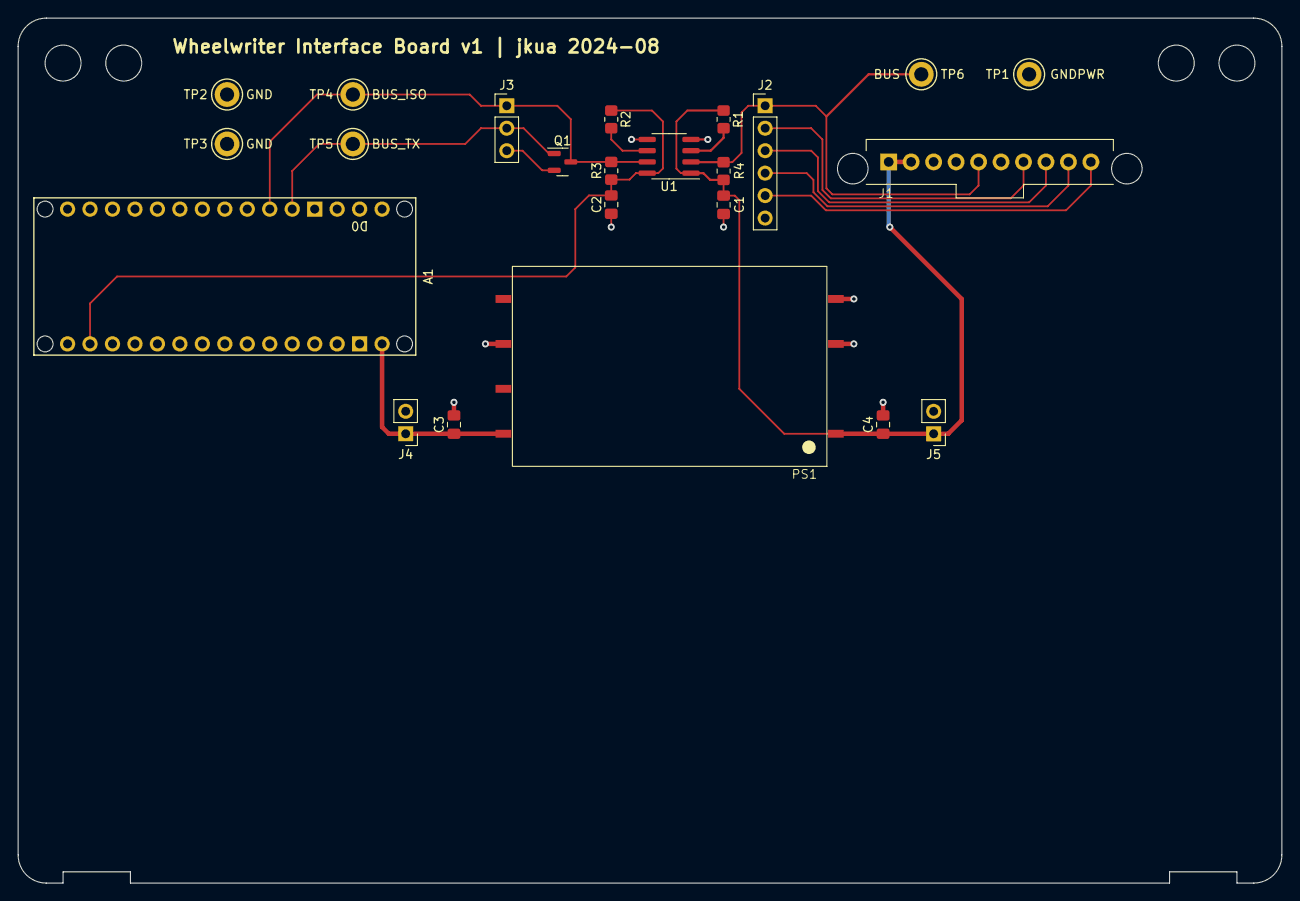
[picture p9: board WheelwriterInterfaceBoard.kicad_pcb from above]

Board: 2 copper layers, 142.9 x 97.8 mm, 27 parts (0 on the bottom side), 14 nets.

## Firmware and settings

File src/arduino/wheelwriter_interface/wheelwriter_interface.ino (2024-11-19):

// Wheelwriter interface for an Arduino Nano RP2040 Connect
// Copyright (c) 2023 John Kua <john@kua.fm>
//

#include <WiFiNINA.h>
#include "ParameterStorage.h"

#include "uart_9bit/Uart9bit.h"
#include "Wheelwriter.h"
#include "WheelwriterCommandLineInterface.h"
#include "WheelwriterRestApi.h"

WiFiServer webServer(80);
ParameterStorage parameterStorage;
Uart9Bit uart;
wheelwriter::Wheelwriter typewriter;
WheelwriterRestApi restApi(webServer, typewriter);
int inByte = 0;
char inputBuffer[65];
wheelwriter::WheelwriterCommandLineInterface serialCli(typewriter, 
                                                       wheelwriter::IF_SERIAL);
wheelwriter::WheelwriterCommandLineInterface typewriterCli(typewriter, 
                                                           wheelwriter::IF_TYPEWRITER);
bool terminalMode = false;

void setup() {
  gpio_set_drive_strength(25, GPIO_DRIVE_STRENGTH_12MA);

  // Level converter output enable - set to disable
  pinMode(6, OUTPUT);
  digitalWrite(6, LOW);

  // UART RX pin - remove when implemented in Uart9Bit
  pinMode(3, INPUT);

  // UART TX
  uint sm_tx = 0;
  uint pin_tx = 25; // D2/GPIO25
  uint sm_rx = 1;
  uint pin_rx = 15; // D3/GPIO15
  uart.init(pio0, sm_tx, pin_tx, sm_rx, pin_rx, 185700);
  typewriter.init(&uart);

  // USB Serial
  Serial.begin(115200);

  // Wait up to one second for serial port to connect
  int count = 1000;
  while (!Serial && count--) {
    delay(1);
  }
  Serial.write("\n");
  Serial.println("#############################");
  Serial.println("### Wheelwriter Interface ###");
  Serial.println("#############################");

  parameterStorage.printBlockDeviceInfo();
  parameterStorage.loadParametersFromFlash();  
  parameterStorage.printParameters();
  Serial.write("\n");

  restApi.init();

  std::string ssid;
  std::string password;
  if (parameterStorage.readParameter("WIFI_SSID", ssid) && 
      parameterStorage.readParameter("WIFI_PASSWORD", password)) {
    Serial.write("--> Connecting to WiFi...\n");
    restApi.connect(ssid.c_str(), password.c_str());
  }
  else {
    Serial.write("--> No WiFi credentials found in flash\n");
  }
  Serial.write("[READY]\n");
}

void loop() {
  while (!Serial.available()) {// && !typewriter.available()) {
    restApi.processClient();
  }

  // while (typewriter.available()) {
  while (false) {
    if (!terminalMode) {
      char ascii;
      wheelwriter::ww_keypress_type keypressType = typewriter.readKeypress(ascii, 0, 0);
      if ((keypressType == wheelwriter::CODE_KEYPRESS) &&
          (ascii == (wheelwriter::SHIFT_MASK | wheelwriter::KEY_I))) {
        if (!terminalMode) {
          while (typewriter.readKeypress(ascii, 0, 0) != wheelwriter::CODE_KEYPRESS) {}
          typewriter.spinWheel();
          terminalMode = true;
          typewriterCli.logInfo("*** Entering terminal mode...\n");
          typewriterCli.print("[READY]\n");
        }
      }
    }
    else { 
      char* line = typewriterCli.readLine();
      ParameterString parameters(line, ' ');
      std::string command = parameters.getParameterString(0);

      if ((command == "h") || (command == "help")) {
        typewriterCli.print("Available functions:\n");
        typewriterCli.print("help - print this help text\n");
        typewriterCli.print("buffer - execute the buffer test\n");
        typewriterCli.print("char - execute the character test\n");
        typewriterCli.print("circle - execute the circle test\n");
        // typewriterCli.print("keyboard - read input from the keyboard\n");
        typewriterCli.print("loopback - execute the loopback test\n");
        typewriterCli.print("query - query typewriter for information\n");
        // typewriterCli.print("raw - send raw commands\n");
        // typewriterCli.print("read - read bus commands\n");
        // typewriterCli.print("relay - relay bus commands\n");
        typewriterCli.print("sample - print a type sample\n");
        // typewriterCli.print("type - type characters on the typewriter\n");
        typewriterCli.print("wifi - set up WiFi\n");
        typewriterCli.print("exit - exit terminal mode\n");
      }
      else if (command == "buffer") {
        uint16_t numChars = parameters.getParameterInt(1, 10);
        uint8_t charsPerLine = parameters.getParameterInt(2, 80);
        
        typewriterCli.print("[FUNCTION] Buffer Test %d / # Characters: %d, Characters Per Line: %d\n", numChars, charsPerLine);
        typewriter.bufferTest(numChars, charsPerLine);
      }
      else if (command == "exit") {
        typewriterCli.print("[END]\n");
        typewriter.spinWheel();
        typewriter.spinWheel();
        terminalMode = false;
        typewriterCli.logInfo("*** Exited terminal mode.\n");
      }
      else {
        typewriterCli.logWarn("Invalid command: %s\n", command.c_str());
        typewriterCli.print("[UNKNOWN FUNCTION] Enter 'help' to see a list of available commands\n");
      }
      if (terminalMode) {
        typewriterCli.print("[READY]\n");
      }
    }
  }

  if (Serial.available() > 0) {
    String inString = Serial.readStringUntil('\n');
    inString.toLowerCase();
    inString.toCharArray(inputBuffer, 65);

    ParameterString parameters(inString.c_str(), ' ');
    std::string command = parameters.getParameterString(0);

    if (command.size() == 0) {
      // Do nothing, loop back to the ready prompt
    }
    else if ((command == "h") || (command == "help")) {
      Serial.write("Available functions:\n");
      Serial.write("help - print this help text\n");
      Serial.write("buffer - execute the buffer test\n");
      Serial.write("char - execute the character test\n");
      Serial.write("circle - execute the circle test\n");
      Serial.write("keyboard - read input from the keyboard\n");
      Serial.write("loopback - execute the loopback test\n");
      Serial.write("query - query typewriter for information\n");
      Serial.write("raw - send raw commands\n");
      Serial.write("read - read bus commands\n");
      Serial.write("relay - relay bus commands\n");
      Serial.write("sample - print a type sample\n");
      Serial.write("type - type characters on the typewriter\n");
      Serial.write("wifi - set up WiFi\n");
    }
    else if (command == "buffer") {
      uint16_t numChars = parameters.getParameterInt(1, 10);
      uint8_t charsPerLine = parameters.getParameterInt(2, 80);
      
      Serial.write("[FUNCTION] Buffer Test ");
      Serial.write("| # Characters: ");
      Serial.print(numChars);
      Serial.write(", Characters Per Line: ");
      Serial.println(charsPerLine);
      typewriter.bufferTest(numChars, charsPerLine);
    }
    else if (command == "char") {
      uint8_t typestyle = wheelwriter::TYPESTYLE_NORMAL;
      std::string param = parameters.getParameterString(1);
      if (param == "bold") {
        typestyle = wheelwriter::TYPESTYLE_BOLD;
      }
      else if (param == "underline") {
        typestyle = wheelwriter::TYPESTYLE_UNDERLINE;
      }

      Serial.write("[FUNCTION] Character Test - ");
      if (typestyle == wheelwriter::TYPESTYLE_NORMAL) {
        Serial.write("Normal\n");
      }
      else {
        if (typestyle & 0x0F) {
          Serial.write("Bold ");
        }
        if (typestyle & 0xF0) {
          Serial.write("Underline");
        }
        Serial.write("\n");
      }
      typewriter.characterTest((wheelwriter::ww_typestyle)typestyle);
    }
    else if (command == "circle") {
      Serial.write("[FUNCTION] Circle Test\n");
      typewriter.circleTest();
    }
    else if (command == "keyboard") {
      uint8_t verbose = 0;
      std::string param = parameters.getParameterString(1);
      if (param == "v") {
        verbose = 1;
      }
      else if (param == "vv") {
        verbose = 2;
      }

      Serial.write("[FUNCTION] Keyboard Input");
      if (verbose == 0) {
        Serial.write('\n');
      }
      else {
        Serial.write(" - verbose: ");
        Serial.println(verbose);
      }
      keyboardFunction(verbose);
    }
    else if (command == "loopback") {
      Serial.write("[FUNCTION] Loopback Test\n");
      loopbackTest();
    }
    else if (command == "query") {
      Serial.write("[FUNCTION] Query\n");
      queryFunction();
    }
    else if (command == "raw") {
      Serial.write("[FUNCTION] Command\n");
      rawCommandFunction();
    }
    else if (command == "read") {
      Serial.write("[FUNCTION] Read Bus\n");
      readFunction();
    }
    else if (command == "relay") {
      Serial.write("[FUNCTION] Relay commands\n");
      relayFunction();
    }
    
    else if (command == "sample") {
      uint8_t plusPosition = parameters.getParameterInt(1, 0x3b);
      uint8_t underscorePosition = parameters.getParameterInt(2, 0x4f);
      
      Serial.write("[FUNCTION] Printwheel Sample ");
      Serial.write("| plus: 0x");
      Serial.print(plusPosition, HEX);
      Serial.write(", - underscore: 0x");
      Serial.println(underscorePosition, HEX);
      typewriter.printwheelSample(plusPosition, underscorePosition);
    }
    else if (command == "type") {
      uint8_t keyboard = parameters.getParameterInt(1, 1);
      uint8_t useCaratAsControl = parameters.getParameterInt(2, 1);

      Serial.write("[FUNCTION] Type ");
      Serial.write("| Keyboard: ");
      Serial.print(keyboard);
      Serial.write(", UseCaratAsControl: ");
      Serial.println(useCaratAsControl);
      typeFunction(keyboard, useCaratAsControl);
    }
    else if (command == "wifi") {
      Serial.write("[FUNCTION] Configure wifi\n");
      char* ssid = (char*)malloc(65);
      char* password = (char*)malloc(65);
      if (connectWifi(ssid, password)) {
        while (true) {
          Serial.print("Write credentials to flash? (y/n) ");
          while (true) {
            if (Serial.available()) {
              inString = Serial.readStringUntil('\n');
              Serial.write('\n');
              break;
            }
          }
          inString.toLowerCase();
          if (inString[0] == 'y') {
            parameterStorage.writeParameter("WIFI_SSID", ssid);
            parameterStorage.writeParameter("WIFI_PASSWORD", password);
            parameterStorage.storeParametersToFlash();
            break;
          }
          else if (inString[0] == 'n') {
            break;
          }
        }
      }
    }
    else {
      Serial.write("[UNKNOWN FUNCTION] Enter 'help' to see a list of available commands\n");
    }
    Serial.write("[READY]\n");
  }
}


void keyboardFunction(uint8_t verbose) {
  typewriter.readFlush();

  Serial.write("[BEGIN]\n");
  while (true) {
    if (Serial.available()) {
      String inString = Serial.readStringUntil('\n');
      inString.toLowerCase();
      inString.toCharArray(inputBuffer, 65);

      // End with 'q' or EOT (CTRL-D)
      if ((strlen(inputBuffer) == 1) && ((inputBuffer[0] == 'q') || (inputBuffer[0] == 0x04))) {
        break;
      }
    }
    char ascii;
    uint8_t blocking = 0;
    wheelwriter::ww_keypress_type keypressType = typewriter.readKeypress(ascii, blocking, verbose);
    if (keypressType == wheelwriter::NO_COMMAND) {
      continue;
    }
    if (keypressType != wheelwriter::NO_KEYPRESS) {
      if (verbose) {
        Serial.write("Keypress: 0x");
        Serial.println(ascii, HEX);
      }
      else {
        Serial.write(ascii);
      }
    }
    else {
      if (verbose == 2) {
        Serial.write("NO_KEYPRESS\n");
      }
    }
  }
  Serial.write("\n[END]\n");
}

void loopbackTest() {
  typewriter.readFlush();

  while (true) {
    Serial.write("\nPress Enter to send query, q to quit...\n");

    while (Serial.available() == 0) {
      delay(100);
    }
    char inByte = Serial.read();
    if (inByte == 'q') {
      while (Serial.available()) {
        Serial.read();
      }
      break;
    }
    else if (inByte == '\n') {
      uint32_t value;
      uint16_t address = 0x121;
      uint16_t command = wheelwriter::QUERY_MODEL;
      Serial.write("Send address: 0x");
      Serial.println(address, HEX);
      uart.write(address);
      delayMicroseconds(150);
      value = uart.read();
      Serial.write("Received: 0x");
      Serial.println(value, HEX);
      delayMicroseconds(150);
      value = uart.read();
      Serial.write("Received: 0x");
      Serial.println(value, HEX);
      
      Serial.write("Send command: 0x");
      Serial.println(command, HEX);
      uart.write(command);
      delayMicroseconds(150);
      value = uart.read();
      Serial.write("Received: 0x");
      Serial.println(value, HEX);
      delayMicroseconds(150);
      value = uart.read();
      Serial.write("Received: 0x");
      Serial.println(value, HEX);
    }
  }
}

void queryFunction() {
  uint16_t model = typewriter.queryModel();
  Serial.write("Model: 0x");
  Serial.println(model, HEX);
  uint16_t wheel = typewriter.queryPrintwheel();
  Serial.write("Wheel: 0x");
  Serial.println(wheel, HEX);
  uint16_t status = typewriter.queryStatus();
  Serial.write("Status: 0x");
  Serial.println(status, HEX);
  // uint16_t operation = typewriter.queryOperation();
  // Serial.write("Operation: 0x");
  // Serial.println(operation, HEX);
}

void rawCommandFunction() {
  typewriter.readFlush();
  Serial.write("[BEGIN]\n");

  while (true) {
    if (Serial.available()) {
      String inString = Serial.readStringUntil('\n');
      inString.toLowerCase();
      inString.toCharArray(inputBuffer, 65);

      // End with 'q' or EOT (CTRL-D)
      if ((strlen(inputBuffer) == 1) && ((inputBuffer[0] == 'q') || (inputBuffer[0] == 0x04))) {
        break;
      }

      const char delim[2] = " ";
      char* token = strtok(inputBuffer, delim);
      char* end;
      uint8_t command[3];
      uint8_t numValidTokens = 0;
      uint8_t error = 0;

      while (token != NULL) {
        long value = strtol(token, &end, 0);
        if (value > 0xff) {
          error = 1;
          Serial.write("ERROR - values must be bytes!\n");
          break;
        }
        if (numValidTokens >= 3) {
          break;
        }
        if (end != token) {
          command[numValidTokens] = value;
          numValidTokens++;
        }
        token = strtok(NULL, delim);
      }
      if (!error) {
        if (numValidTokens == 1) {
          typewriter.sendCommand((wheelwriter::ww_command)command[0]);
        }
        if (numValidTokens == 2) {
          typewriter.sendCommand((wheelwriter::ww_command)command[0], command[1]);
        }
        if (numValidTokens == 3) {
          typewriter.sendCommand((wheelwriter::ww_command)command[0], command[1], command[2]);
        }
      }
    }
  }

  Serial.write("[END]\n");
}

void readFunction() {
  typewriter.readFlush();
  Serial.write("[BEGIN]\n");
  unsigned long lastCommandTime = 0;
  while (true) {
    if (Serial.available()) {
      String inString = Serial.readStringUntil('\n');
      inString.toLowerCase();
      inString.toCharArray(inputBuffer, 65);

      // End with 'q' or EOT (CTRL-D)
      if ((strlen(inputBuffer) == 1) && ((inputBuffer[0] == 'q') || (inputBuffer[0] == 0x04))) {
        break;
      }
    }
    // typewriter.readFlush();
    uint8_t blocking = 0;
    uint8_t verbose = 1;
    uint8_t commandLength = typewriter.readCommand(blocking, verbose);

    if (commandLength) {
      lastCommandTime = millis();
    }
    if (lastCommandTime && ((millis() - lastCommandTime) > 1000)) {
      Serial.write('\n');
      lastCommandTime = 0;
    }
  }
  
  Serial.write("\n[END]\n");
}

void relayFunction() {
  typewriter.readFlush();
  Serial.write("[BEGIN]\n");
  unsigned long commandStartTime, commandDuration;
  unsigned long timeout = 1000;
  unsigned char inByte;
  unsigned char response[4];
  while (true) {
    if (Serial.available()) {
      commandStartTime = millis();

      // Read the command byte and hand off to the respective handlers
      inByte = Serial.read();
      if (inByte == 0x04) { // ^D, end mode
        break;
      }
      if (inByte == 0x0a) { // \n, NOOP
        continue;
      }
      if (inByte & 0x10) {
        relayCommand(inByte, commandStartTime, timeout);
        continue;
      }
      if (inByte & 0x80) {
        //configCommand(inByte, commandStartTime, timeout);
        continue;
      }

      // Unknown command byte - read until \n and return error
      response[0] = inByte; // Command byte we are responding to
      response[1] = 0xf0;   // Invalid command response
      response[2] = inByte;
      response[3] = '\n';
      while (true) {
        if (Serial.available()) {
          inByte = Serial.read();
          if (inByte == '\n') {
            break;
          }
        }
        commandDuration = millis() - commandStartTime;
        if (commandDuration > timeout) {
          break;
        }
      }
      Serial.write(response, 4);
    }
  }
  Serial.write("\n[END]\n");
}

void relayCommand(char commandByte, unsigned long commandStartTime, unsigned long timeout) {  
  bool abbreviatedFlag = (commandByte & 0x01);
  bool batchFlag = (commandByte & 0x02);
  bool ignoreErrorsFlag = (commandByte & 0x04);

  unsigned char batchSize = 1;
  
  // In batch mode, read the batch size
  if (batchFlag) {
    while (true) {
      if (Serial.available()) {
        batchSize = Serial.read();
        break;
      }
      if (timeoutCheckAndRespond(commandStartTime, timeout, commandByte)) {
        return;
      }
    }
  }

  // Read and relay the commands
  unsigned char commandBuffer[4];
  unsigned char response[4];
  response[0] = commandByte;
  response[1] = 0x10;
  response[3] = '\n';
  int bytesRead, expectedBytes;
  if (abbreviatedFlag) {
    commandBuffer[0] = typewriter.getDefaultAddress();
  }
  for (unsigned char i = 0; i < batchSize; i++) {
    if (abbreviatedFlag) {
      expectedBytes = 3;
      bytesRead = Serial.readBytes(commandBuffer+1, expectedBytes);
    }
    else {
      expectedBytes = 4;
      bytesRead = Serial.readBytes(commandBuffer, expectedBytes);
    }
    if (bytesRead < expectedBytes) {
      sendTimeoutResponse(commandByte);
      return;
    }
    uint8_t error, failIndex;
    // Serial.write("Sending command\n");
    // Serial.write(commandBuffer, 4);
    // Serial.write('\n');
    uint8_t wwCmdResponse = typewriter.sendCommand(commandBuffer[0], commandBuffer[1], commandBuffer[2], commandBuffer[3], error, failIndex, (int)ignoreErrorsFlag);
    if (!ignoreErrorsFlag && error) {
        if (batchFlag) {
          response[1] = 0x12; // Batch error
          response[2] = i;    // Failed command index
        }
        else {
          response[1] = error;      // Command error code
          response[2] = failIndex;  // Command byte that failed
        }
        Serial.write(response, 4);
        return;
    }
    else {
      response[2] = wwCmdResponse;
    }
  }

  // Read terminator
  // Serial.write("Reading terminator\n");
  unsigned char inByte;
  bytesRead = Serial.readBytes(&inByte, 1);
  // Serial.write("bytesRead: ");
  // Serial.write(bytesRead);
  // Serial.write('\n');
  if (bytesRead) {
    // Serial.write("inByte: ");
    // Serial.write(inByte);
    // Serial.write('\n');
    if (inByte != '\n') {
      response[1] = 0x15; // Command length error
      response[2] = expectedBytes * batchSize;  // Expected length
    }
    Serial.write(response, 4);
  }
  else {
    sendTimeoutResponse(commandByte);
  }
  return;
}

int timeoutCheckAndRespond(unsigned long commandStartTime, unsigned long timeout, unsigned char commandByte) {
  unsigned long commandDuration = millis() - commandStartTime;
  if (commandDuration > timeout) {
    sendTimeoutResponse(commandByte);
    return 1;
  }
  else {
    return 0;
  }
}

void sendTimeoutResponse(unsigned char commandByte) {
  unsigned char response[4];
  response[0] = commandByte;  // Command byte we are responding to
  response[1] = 0xf2;         // Command transmission timeout
  response[2] = commandByte;
  response[3] = '\n';
  Serial.write(response, 4);
}

void typeFunction(uint8_t keyboard, uint8_t useCaratAsControl) {
  uint8_t bytesAvailable = 0;
  uint8_t paused = false;

  typewriter.setSpaceForWheel();
  typewriter.setKeyboard(keyboard);
  typewriter.setLeftMargin();

  typewriter.typeStream.reset();
  typewriter.typeStream.setUseCaratAsControl(useCaratAsControl);

  Serial.write("[BEGIN]\n");

  while (true) {
    bytesAvailable = Serial.available();

    // Flow control
    if (bytesAvailable > 48) {
      Serial.write(0x13); // XOFF
      paused = true;
    }
    else if (paused && (bytesAvailable < 16)) {
      Serial.write(0x11); // XON
      paused = false;
    }

    if (bytesAvailable) {
      char inByte = Serial.read();
      if (!(typewriter.typeStream << inByte)) {
        break;
      }
    }
  }

  Serial.write("\n[END]\n");
}
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

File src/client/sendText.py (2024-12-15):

#!/usr/bin/env python3

import serial
import time
import sys

from wheelwriterClient import WheelwriterInterface, WWTypeMode

if __name__=='__main__':
	import argparse
	parser = argparse.ArgumentParser()
	parser.add_argument('--device', '-d', required=True, help='Serial port to connect to')
	parser.add_argument('file', help='Text file to send')
	parser.add_argument('--endlines', '-e', type=int, default=0, help='Additional carriage returns at the end')
	parser.add_argument('--keyboard', '-k', type=int, choices=[1, 103], default=1, help='Keyboard layout')
	parser.add_argument('--noPrintableEscape', action='store_true', help='Do not allow printable escape sequence ^[, binary only')
	args = parser.parse_args()

	with WheelwriterInterface(args.device) as interface:
		with WWTypeMode(interface, args.keyboard, args.noPrintableEscape) as typeMode:
			typeMode.sendTextFile(args.file, endLines=args.endlines)

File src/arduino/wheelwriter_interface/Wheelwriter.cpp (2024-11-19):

// Wheelwriter class for an IBM Wheelwriter
// via the option interface
//
// Copyright (c) 2023 John Kua <john@kua.fm>
//
#include "Wheelwriter.h"
#include <Arduino.h>

using namespace wheelwriter;

uint8_t Wheelwriter::sendCommand(ww_command command) {
	uint8_t error, failIndex;
	uint8_t response = sendCommand(defaultAddress_, command, 0, 0, error, failIndex, 0);
	if (error) {
		_printCommandError(error, failIndex, response);
		return 0;
	}
	return (uint8_t)response;
}
uint8_t Wheelwriter::sendCommand(ww_command command, uint8_t data) {
	uint8_t error, failIndex;
	uint8_t response = sendCommand(defaultAddress_, command, data, 0, error, failIndex, 0);
	if (error) {
		_printCommandError(error, failIndex, response);
		return 0;
	}
	return (uint8_t)response;
}
uint8_t Wheelwriter::sendCommand(ww_command command, uint8_t data1, uint8_t data2) {
	uint8_t error, failIndex;
	uint8_t response = sendCommand(defaultAddress_, command, data1, data2, error, failIndex, 0);
	if (error) {
		_printCommandError(error, failIndex, response);
		return 0;
	}
	return (uint8_t)response;
}
inline void Wheelwriter::_printCommandError(uint8_t error, uint8_t failIndex, uint16_t response) {
	switch (error) {
		case 0x11:
			Serial.write("ERROR: sendCommand(): receive bad ACK to ");
			Serial.write(ww_command_part_strings[failIndex]);
			Serial.write(" byte! 0x");
			Serial.println(response, HEX);
		case 0x13:
			Serial.write("ERROR: sendCommand(): invalid command! 0x");
			Serial.println(response, HEX);
	}
}
inline uint16_t Wheelwriter::_sendByte(uint16_t byte) {
	uart_->write(byte);
	uart_->read(); // Ignore self-transmission
	return uart_->read();
}
uint16_t Wheelwriter::sendCommand(uint8_t address, uint8_t command, uint8_t data1, uint8_t data2, uint8_t& error, uint8_t& failIndex, int ignoreErrors) {
	// Ensure the typewriter is ready
	waitReady((ww_command)command);
	
	return _sendCommand(address, command, data1, data2, error, failIndex, ignoreErrors);
}
uint16_t Wheelwriter::_sendCommand(uint8_t address, uint8_t command, uint8_t data1, uint8_t data2, uint8_t& error, uint8_t& failIndex, int ignoreErrors) {
	error = 0;
	failIndex = 0;

	// Check if command is valid
	if (command > WW_MAX_VALID_COMMAND) {
		error = 0x13;
		return command;
	}
	uint8_t commandLength = ww_command_length[command];

	uint16_t addressOut = address + WW_ADDRESS_BIT;
	uint16_t response;
	
	// Send address
	response = _sendByte(addressOut);
	if (!ignoreErrors && (response != 0)) { // Bad ACK
		error = 0x11;
		failIndex = 0;
		return response;
	}

	// Send command
	response = _sendByte(command);
	if (commandLength == 1) {
		return response;
	}
	if (!ignoreErrors && (response != 0)) { // Bad ACK
		error = 0x11;
		failIndex = 1;
		return response;
	}

	// Send data 1
	response = _sendByte(data1);
	if (commandLength == 2) {
		return response;
	}
	if (!ignoreErrors && (response != 0)) { // Bad ACK
		error = 0x11;
		failIndex = 2;
		return response;
	}

	// Send data 2
	return _sendByte(data2);
}

uint8_t Wheelwriter::readCommand(uint8_t blocking, uint8_t verbose) {
	uint16_t response;

	// Address
	if ((blocking == 0) && (!uart_->available())) {
		return 0;
	}
	unsigned long startTime = millis();
	bufferIn_[0] = uart_->read();
	
	if (bufferIn_[0] != 0x121) {
		if (verbose == 2) {
			sprintf(stringBuffer, "\nERROR: readCommand(): expected address byte = 0x121! Got 0x%03x\n", bufferIn_[0]);
			Serial.write(stringBuffer);
		}
		return 0;
	}
	if (verbose) {
		sprintf(stringBuffer, "[%d] ADR 0x%03x", startTime, bufferIn_[0]);
		Serial.write(stringBuffer);
	}

	// Address ACK
	response = uart_->read();
	if (response != 0) {
		if (verbose == 2) {
			sprintf(stringBuffer, "\nERROR: readCommand(): expected address ACK = 0! Got 0x%02x\n", response);
			Serial.write(stringBuffer);
		}
		return 0;
	}

	// Command
	bufferIn_[1] = uart_->read();
	if (bufferIn_[1] > 0xe) {
		if (verbose == 2) {
			sprintf(stringBuffer, "\nERROR: readCommand(): expected command < 0x0f! Got 0x%02x\n", bufferIn_[1]);
			Serial.write(stringBuffer);
		}
		return 0;
	}
	if (verbose) {
		sprintf(stringBuffer, ", CMD: 0x%02x", bufferIn_[1]);
		Serial.write(stringBuffer);
	}

	uint8_t commandLength = ww_command_length[bufferIn_[1]];

	// Command ACK
	response = uart_->read();
	if (commandLength == 1) {
		if (verbose) {
			sprintf(stringBuffer, ", RSP: 0x%02x (%d ms)\n", response, millis()-startTime);
			Serial.write(stringBuffer);
		}
		return commandLength;
	}
	if ((commandLength > 1) && (response != 0)) {
		if (verbose == 2) {
			sprintf(stringBuffer, "\nERROR: readCommand(): expected command ACK = 0! Got 0x%02x\n", response);
			Serial.write(stringBuffer);
		}
		return 0;	
	}

	// Data1
	bufferIn_[2] = uart_->read();
	if (verbose) {
		sprintf(stringBuffer, ", DT1: 0x%02x", bufferIn_[2]);
		Serial.write(stringBuffer);
	}

	// Data1 ACK
	response = uart_->read();
	if (commandLength == 2) {
		if (verbose) {
			sprintf(stringBuffer, ", RSP: 0x%02x (%d ms)\n", response, millis()-startTime);
			Serial.write(stringBuffer);
		}
		return commandLength;
	}
	if ((commandLength > 2) && (response != 0)) {
		if (verbose == 2) {
			sprintf(stringBuffer, "\nERROR: readCommand(): expected data1 ACK = 0! Got 0x%02x\n", response);
			Serial.write(stringBuffer);
		}
		return 0;	
	}

	// Data2
	bufferIn_[3] = uart_->read();
	if (verbose) {
		sprintf(stringBuffer, ", DT2: 0x%02x", bufferIn_[3]);
		Serial.write(stringBuffer);
	}

	// Data2 ACK
	response = uart_->read();
	if (commandLength == 3) {
		if (verbose) {
			sprintf(stringBuffer, ", RSP: 0x%02x (%d ms)\n", response, millis()-startTime);
			Serial.write(stringBuffer);
		}
		return commandLength;
	}
	if ((commandLength > 3) && (response != 0)) {
		if (verbose == 2) {
			sprintf(stringBuffer, "\nERROR: readCommand(): expected data2 ACK = 0! Got 0x%02x\n", response);
			Serial.write(stringBuffer);
		}
		return 0;	
	}
}
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

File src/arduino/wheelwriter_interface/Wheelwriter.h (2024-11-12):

// Wheelwriter class to control an IBM Wheelwriter
// via the option interface
//
// Copyright (c) 2023 John Kua <john@kua.fm>
//
#pragma once

#include "uart_9bit/Uart9bit.h"
#include <string>

namespace wheelwriter {

enum ww_model {
	UNKNOWN_MODEL = 0x00,
	WHEELWRITER_3 = 0x06,
	WHEELWRITER_5 = 0x25,
	WHEELWRITER_6 = 0x26
};

enum ww_command {
	QUERY_MODEL = 0x00,
	RESET = 0x01,
	TYPE_CHARACTER_NO_ADVANCE = 0x02,
	TYPE_CHARACTER_AND_ADVANCE = 0x03,
	ERASE_CHARACTER_AND_ADVANCE = 0x04,
	MOVE_PLATEN = 0x05,
	MOVE_CARRIAGE = 0x06,
	SPIN_WHEEL = 0x07,
	QUERY_WHEEL = 0x08,
	SET_REPEAT_MODE = 0x09,
	UNKNOWN_0A = 0x0a,
	QUERY_STATUS = 0x0b,
	UNKNOWN_0C = 0x0c,
	QUERY_OPERATION = 0x0d,
	SEND_CODE = 0x0e,
};

// Index is command value
// 0: Unknown command
// 1: Just the command is sent
// 2: Command + Data 1
// 3: Command + Data 2
static const uint8_t ww_command_length[16] = {1, 1, 3, 3, 
																				3, 2, 3, 1, 
																				1, 2, 2, 1,
																				3, 2, 2, 0};

static const char ww_command_part_strings[][8] = {
	"address",
	"command",
	"data1",
	"data2"
};
enum ww_platen_direction {
	PLATEN_DIRECTION_DOWN = 0x00,
	PLATEN_DIRECTION_UP = 0x80
};

enum ww_carriage_direction {
	CARRIAGE_DIRECTION_LEFT = 0x00,
	CARRIAGE_DIRECTION_RIGHT = 0x80
};

enum ww_printwheel {
	PROPORTIONAL = 0x08,
	CPI_15 = 0x10,
	CPI_12 = 0x20,
	NO_WHEEL = 0x21,
	CPI_10 = 0x40
};

enum ww_keyboard {
	KEYBOARD_US = 1,
	KEYBOARD_ASCII = 103,
	KEYBOARD_USSR = 231
};

enum ww_repeat_mode {
	REPEAT_OFF = 0x00,
	SHIFT_RIGHT_HALF_SPACE = 0x02,
	UNDERLINE = 0x04,
	REPEAT_CHARACTER = 0x08,
	CENTER = 0x80,
};

enum ww_status {
	NO_STATUS = 0x00,
	CARRIAGE_MOTION_COMPLETE = 0x04,
	PAPER_DOWN = 0x10,
	CARRIAGE_MOTION_2 = 0x14,
	PRINTWHEEL_CHANGE = 0x40
};

enum ww_operation {
	NO_OPERATION = 0x00,
	BACKSPACE = 0x04,
	ERASE = 0x05,
	CARRIAGE_RETURN = 0x07,
	TAB = 0x0a,
	TAB_SET = 0x12
};

enum ww_keycode {	// Mapped with a Wheelwriter 3 keyboard
  KEY_A = 0x04,
	KEY_B = 0x1f,
	KEY_C = 0x16,	// CTR
	KEY_D = 0x14,
	KEY_E = 0x12,
	KEY_F = 0x1c,
	KEY_G = 0x1d,
	KEY_H = 0x25,
	KEY_I = 0x2a,
	KEY_J = 0x24,
	KEY_K = 0x2c,
	KEY_L = 0x34,
	KEY_M = 0x26,
	KEY_N = 0x72,	// CAPS
	KEY_O = 0x32,
	KEY_P = 0x3a,
	KEY_Q = 0x02,	// Impression control?
	KEY_R = 0x1a,
	KEY_S = 0x0c,
	KEY_T = 0x1b,
	KEY_U = 0x22,  // UNDLN
	KEY_V = 0x1e,
	KEY_W = 0x0a,
	KEY_X = 0x0e,
	KEY_Y = 0x23,
	KEY_Z = 0x06,
	KEY_0 = 0x39,
	KEY_1 = 0x01,	// Spell check on/off
	KEY_2 = 0x09,	// Spell check - add word to dictionary
	KEY_3 = 0x11,  // Spell check - delete word from dictionary
	KEY_4 = 0x19,	// Spell check - adjust beep volume
	KEY_5 = 0x18,	// Printer on/off
	KEY_6 = 0x20,	// Printer - online
	KEY_7 = 0x21,	// Printer - feed
	KEY_8 = 0x29,	// Printer - set
	KEY_9 = 0x31,

	KEY_PLUS_MINUS = 0x00,
	KEY_HYPHEN = 0x38,
	KEY_EQUAL = 0x28,
	KEY_BACKSPACE = 0x50,			// BKSP 1/2
	KEY_TAB = 0x4a,
	KEY_HALF = 0x3b,		  			// ^2
	KEY_RIGHT_BRACKET = 0x2b,	// ^3
	KEY_RETURN = 0x56,
	KEY_SEMICOLON = 0x3c,			// Section mark
	KEY_APOSTROPHE = 0x3d,			// Paragraph mark
	KEY_COMMA = 0x2e,
	KEY_PERIOD = 0x36,
	KEY_SLASH = 0x3f,
	KEY_SPACE = 0x47,
	KEY_ERASE = 0x4f,

	KEY_MARGIN_RELEASE = 0x48,
	KEY_LEFT_MARGIN = 0x42,
	KEY_RIGHT_MARGIN = 0x4b,
	KEY_TAB_SET = 0x4c,
	KEY_TAB_CLEAR = 0x45,

	KEY_PAPER_UP = 0x51,
	KEY_PAPER_DOWN = 0x52,
	KEY_MICRO_UP = 0x54,
	KEY_MICRO_DOWN = 0x46,
	KEY_LINE_SPACE = 0x57,

	PAPER_FEED_LEVER = 0x49,

	SHIFT_MASK = 0x80,	  // High bit indicates Shift pressed or Shift locked
	CODE_KEY_RELEASED = 0x67 // Emitted when the Code key is released
};

enum ww_typestyle {
	TYPESTYLE_NORMAL = 0x00,
	TYPESTYLE_BOLD = 0x01,
	TYPESTYLE_UNDERLINE = 0x10,
	TYPESTYLE_BOLD_UNDERLINE = 0x11
};

enum ww_linespacing {
	LINESPACING_ONE = 0x00,
	LINESPACING_ONE_POINT_FIVE = 0x01,
	LINESPACING_TWO = 0x02,
	LINESPACING_THREE = 0x03
};

enum ww_keypress_type {
	NO_KEYPRESS = 0x00,
	CHARACTER_KEYPRESS = 0x01,
	SPACE_KEYPRESS = 0x02,
	RETURN_KEYPRESS = 0x03,
	CODE_KEYPRESS = 0x04,
	NO_COMMAND = 0xff
};

static const uint16_t WW_ADDRESS_BIT = 0x100;
static const uint8_t WW_MOTOR_CTRL_ADDR = 0x21;
static const uint8_t WW_PRINTWHEEL_MAX = 0x60;
static const uint8_t WW_CARRIAGE_ADVANCE_USTEP_MAX = 63;
static const uint8_t WW_PLATEN_ADVANCE_USTEP_MAX = 127;
static const uint8_t WW_MAX_VALID_COMMAND = SEND_CODE;
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

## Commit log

2023-01-29 Added Wheelwriter hardware doc
2023-01-29 Add connector labels to hardware block diagram
2023-02-01 Initial Arduino Nano RP2040 Connect code. Basic interface to send commands to the typewriter implemented
2023-02-01 Added docs for the Wheelwriter bus and the Arduino code
2023-02-06 TX works - can generate circle test! RX does not work
    [Wheelwriter.cpp, Wheelwriter.h, wheelwriter_interface.ino]
2023-02-07 Minor test string fix
    [wheelwriter_interface.ino]
2023-02-08 Moved uart_9bit files to a separate folder
2023-02-09 Added raw and printwheel sample modes to the Arduino
    Also added carriage position tracking to automate carriage returns.
    Added character space automation and linefeed automation.
    Added sendText.py Python client to upload text to the typewriter.
    This includes some sample text.
2023-02-10 UART RX works!
    Implemented ACK and response reads and added typewriter status
    checks so that the delays can be stripped out and typing happens
    at full speed.
    Loopback and model query tests added. Type function seems to be
    broken. Occasionally getting the odd ACK error getting the address
    indicating a sync error. Need to disable the receiver during TX.
    Also fixed the ANSI escape commands in the text samples, but only
    seeing bold and not underline.
    [Wheelwriter.cpp, Wheelwriter.h, sendText.py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]
2023-02-10 Disabled the Wheelwriter::queryOperation() method. It's not a query and it's unclear what it actually does
2023-02-11 Stripped out the waitReady() calls as the typewriter appears to have a reasonably deep command buffer. Also fixed the queryPrintwheel() and queryStatus() calls to actually output something
    [Wheelwriter.cpp, wheelwriter_interface.ino]
2023-02-11 sendText.py working now
    Added ANSI test file. Removed title underline from other text samples.
    Added Wheelwriter::readFlush() to try to clean up/diagnose a problem
    where the serial comms get out of sync and misses a read.
    [Wheelwriter.cpp, Wheelwriter.h, sendText.py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]
2023-02-12 Added char/line spacing setup based on reading the wheel pitch.Also added a command read function
2023-12-11 Added read flushes to synchronize Arduino with typewriter. Also added printwheel mappings
    [wheelwriter_printwheel_mapping.tsv]
2023-12-11 Added USSR/Cyrillic (231) keyboard
    [wheelwriter_printwheel_mapping.tsv]
2024-07-06 Added PCB board outline
    [WheelwriterInterfaceBoard.kicad_pcb, WheelwriterInterfaceBoard.kicad_sch]
2024-07-06 Added scan of PCB
2024-08-04 PCB v1.0
    [WheelwriterInterfaceBoard.csv, WheelwriterInterfaceBoard.kicad_pcb, WheelwriterInterfaceBoard.kicad_sch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]
2024-08-10 Added schematic PDF and image of PCB
2024-08-19 Arduino: typeFunction() takes useCaratAsControl as an argument
2024-08-19 Arduino - Wheelwriter.cpp fixed and cleaned up readCommand()
    [Wheelwriter.cpp, Wheelwriter.h, wheelwriter_interface.ino]
2024-08-20 Moved Wheelwriter Interface Board v2 to a subfolder of pcb and added the V1 schematic
    [WheelwriterInterfaceBoard.csv, WheelwriterInterfaceBoard.kicad_pcb, WheelwriterInterfaceBoard.kicad_sch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]
2024-08-20 Added pcb README
2024-08-20 Added image to pcb README
2024-08-20 sendText: Added noPrintableEscape option to prevent trigging escape sequences when sending arbitrary ASCII text
    [sendText.py]
2024-08-24 Added draft of the relay protocol document
2024-08-24 Restructured the relay protocol doc and added relay configuration commands
2024-08-24 Relay protocol doc: bullets
2024-08-24 Relay protocol doc: example ticks
2024-08-24 Relay protocol doc: get/set address command byte typos
2024-08-24 Relay protocol doc: panic response
2024-08-24 Relay protocol doc: significant modifications to apply more consistent byte structures
2024-08-24 Relay protocol doc: minor fixes
2024-08-24 Relay protocol doc: Extended the response message to echo the original command byte
2024-08-25 Implemented command relay function - tested with query command
2024-08-25 Extended relayTest to test abbreviated and batch modes - works
2024-08-26 Added the Python WheelwriterClent class and scripts readBus and relayClientTest
2024-08-26 Moved the old WheelwriterClient class to WheelwriterInterface and created a new WheelwriterClient class. Added the clientTest script
2024-08-27 Extended the Python WheelwriterClient with essentially all the commands in the Arduino Wheelwriter class. clientTest now also executes the circle test.
2024-09-02 Added printWheelPositions.py to send wheel positions rather than ASCII characters to the typewriter
2024-09-21 Added images of the Wheelwriter expansion housing and some expansion cable information
2024-09-22 Refactored sendText.py to use WheelwriterInterface
2024-09-23 Added support for fractional character/line space movements in the Python WheelwriterClient. Also added interleave support in printWheelPositions.py
2024-10-21 Update pcb README.md
2024-10-31 Refactored typeFunction() to move the majority of processing into the Wheelwriter::TypeStream class so that the REST API can also use it. Also moved the bufferTest() into Wheelwriter as well and fixe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
    [PicoRest.cpp, Wheelwriter.cpp, Wheelwriter.h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]
2024-11-01 Fixed an issue in Wheelwriter::TypeStream::parseEscape() where some invalid CSI escape sequences were not caught
    [Wheelwriter.cpp, Wheelwriter.h]
2024-11-01 Added /characterTest, /circleTest, /printwheelSample, and /query endpoints to the REST API. Added ParameterString class to handle parsing delimited lists of parameters
2024-11-02 Added 'corrected' option to /readLine
    [Wheelwriter.cpp, Wheelwriter.h]
2024-11-10 Refactored Wheelwriter::sendCommand() methods and added readFlush() and queryStatus() before all commands. Stripped out some superfluous readFlush() calls in the rest of the code
2024-11-12 Added WheelwriterCommandLineInterface class to handle stuff. Changed code+key mappings to just key mappings. Added documentation on Wheelwriter bus commands.
2024-12-15 wheelwriterClient TypeMode - Added back support for keyboard and noPrintableEscape options that were lost in the refactor
